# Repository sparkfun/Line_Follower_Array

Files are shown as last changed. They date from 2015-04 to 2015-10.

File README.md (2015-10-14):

SparkFun Line Follower Array
========================================

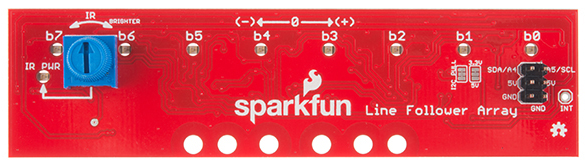
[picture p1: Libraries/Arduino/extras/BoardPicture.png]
SparkFun Line Follower Array


[*SparkFun Line Follower Array (SEN-13582)*](https://www.sparkfun.com/products/13582)

The Sensor Bar takes an 8 bit reading of reflectance for use with following lines or reading dark/light patterns.  The bar can see from about 1/4 to 3/4 inches away.  IR illumination power can be adjusted with the on-board potentiometer.  Illumination can be turned on and off with software to conserve power, or left on all the time for faster readings.

Repository Contents
-------------------

* **/Documentation** - Data sheets, additional product information
* **/Hardware** - Eagle design files (.brd, .sch)
* **/Libraries** - Libraries for use with the RedBot Line Follower Sensor Bar
* **/Production** - Production panel files (.brd)

Documentation
--------------
* **[Library](https://github.com/sparkfun/SparkFun_Line_Follower_Array_Arduino_Library)** - Arduino library for the array.
* **[Hookup Guide](https://learn.sparkfun.com/tutorials/sparkfun-line-follower-array-hookup-guide)** - Basic hookup guide for the array.

Product Versions
----------------
* [*SparkFun Line Follower Array (SEN-13582)*](https://www.sparkfun.com/products/13582)

Version History
---------------
* [V_0.4.0](https://github.com/sparkfun/Line_Follower_Array/tree/V_0.4.0) - Last proto version 
* [V_1.0.0](https://github.com/sparkfun/Line_Follower_Array/tree/V_1.0.0) - Release version

License Information
-------------------

This product is _**open source**_! 

Please review the LICENSE.md file for license information. 

If you have any questions or concerns on licensing, please contact techsupport@sparkfun.com.

Distributed as-is; no warranty is given.

- Your friends at SparkFun.

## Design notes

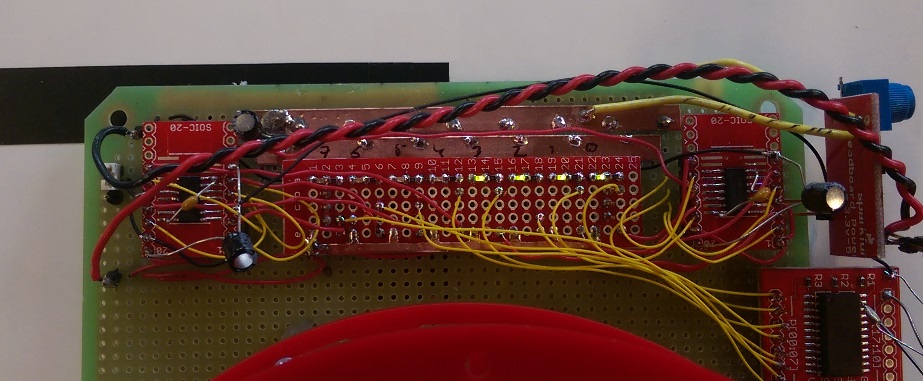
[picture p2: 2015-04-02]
Pictures/left4.jpg

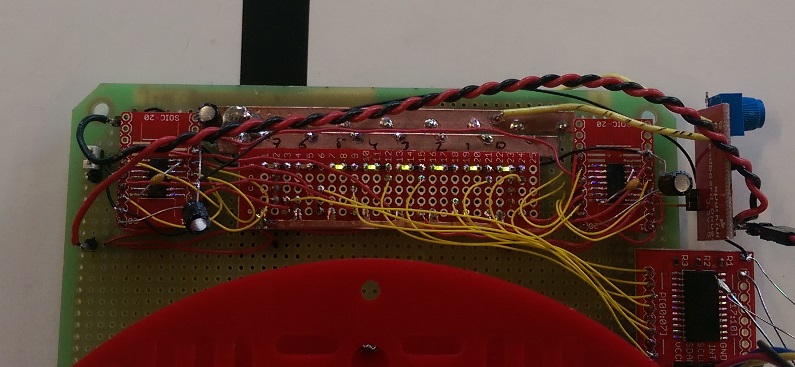
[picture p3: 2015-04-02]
Pictures/left2.jpg

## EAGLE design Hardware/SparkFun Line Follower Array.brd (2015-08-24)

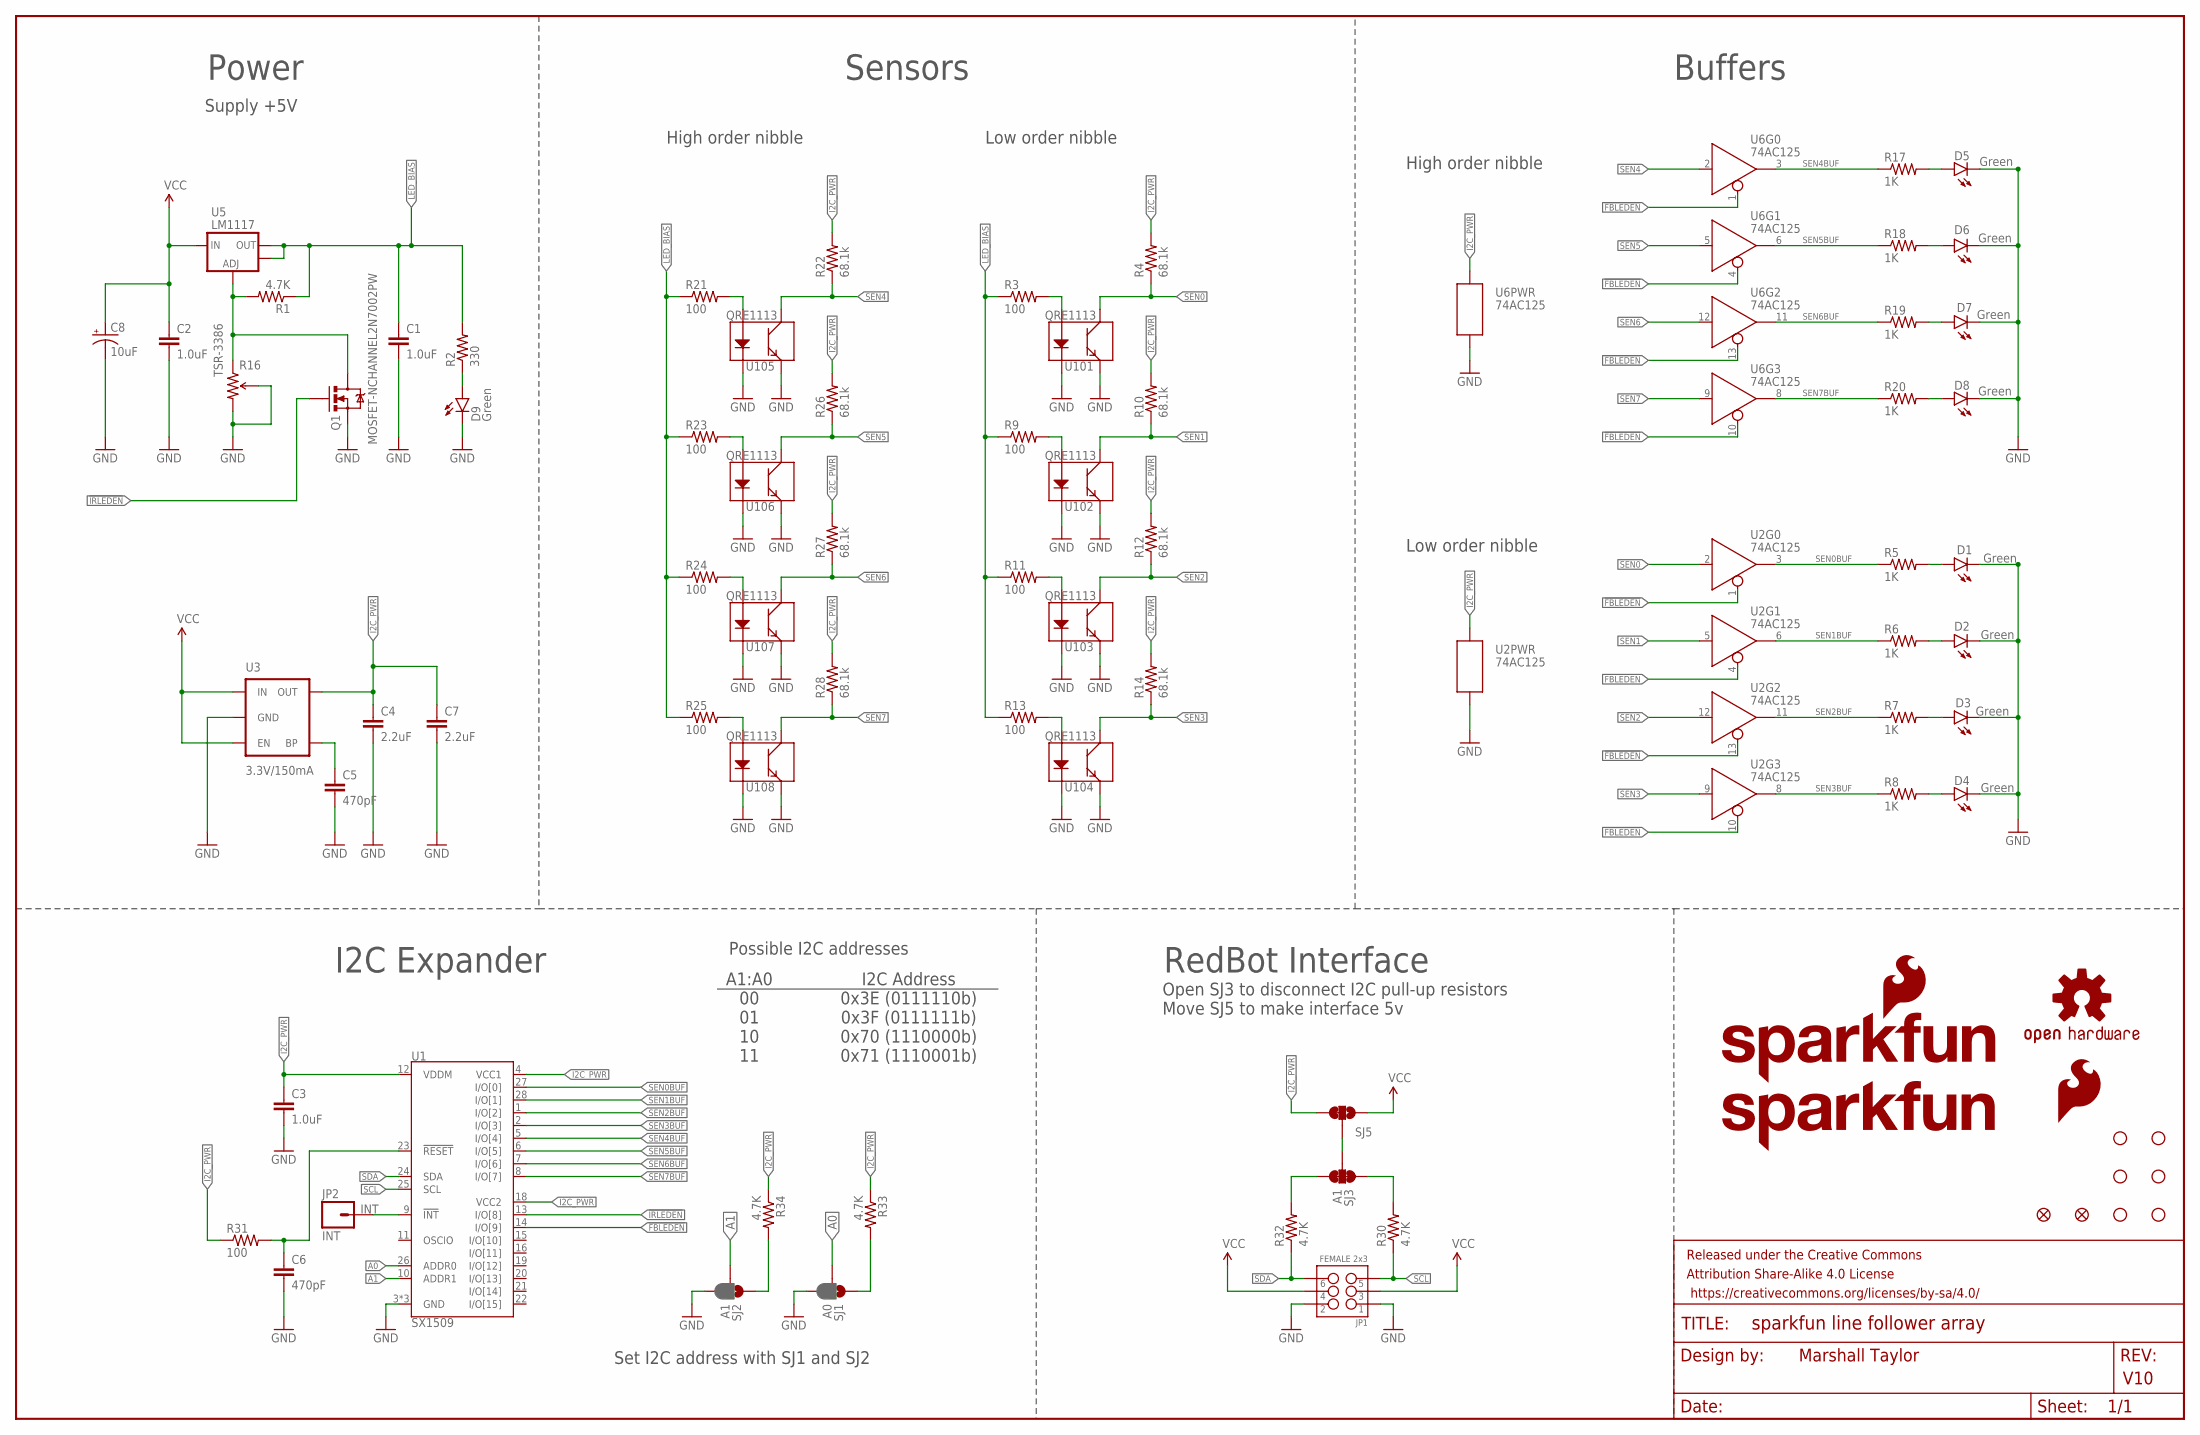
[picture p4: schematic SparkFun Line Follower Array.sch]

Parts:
C1, C2, C3: 1.0uF; 0603-CAP
C4, C7: 2.2uF; 0603-CAP
C5, C6: 470pF; 0603-CAP
C8: 10uF; EIA3216
D1, D2, D3, D4, D5, D6, D7, D8, D9: Green; LED-1206-BOTTOM
FID1, FID2: FIDUCIALUFIDUCIAL; MICRO-FIDUCIAL
FRAME2: FRAME-LEDGER; CREATIVE_COMMONS
JP1: FEMALE 2x3; 2X3
JP2: INT; 1X01
LOGO1: SFE_LOGO_NAME_FLAME.2_INCH; SFE_LOGO_NAME_FLAME_.2
LOGO2: SFE_LOGO_NAME.2_INCH; SFE_LOGO_NAME_.2
LOGO5: SFE_LOGO_FLAME.3_INCH; SFE_LOGO_FLAME_.3
LOGO6: OSHW-LOGOS; OSHW-LOGO-S
Q1: MOSFET-NCHANNEL2N7002PW; SOT323
R1, R30, R32, R33, R34: 4.7K; 0603-RES
R2: 330; 0603-RES
R3, R9, R11, R13, R21, R23, R24, R25, R31: 100; 0603-RES
R4, R10, R12, R14, R22, R26, R27, R28: 68.1k; 0603-RES
R5, R6, R7, R8, R17, R18, R19, R20: 1K; 0603-RES
R16: TSR-3386; 3386U
SJ1: A0; PAD-JUMPER-3-2OF3_NC_BY_PASTE_YES_SILK_FULL_BOX
SJ2: A1; PAD-JUMPER-3-2OF3_NC_BY_PASTE_YES_SILK_FULL_BOX
SJ3: A1; PAD-JUMPER-3-3OF3_NC_BY_TRACE_YES_SILK_FULL_BOX
SJ5: JUMPER-PAD-3-2OF3_NC_BY_TRACE_SMALL; PAD-JUMPER-3-2OF3_NC_BY_TRACE_YES_SILK_FULL_BOX
STANDOFF1, STANDOFF2, STANDOFF3, STANDOFF4, STANDOFF5, STANDOFF6: STAND-OFF
U1: SX1509; QFN-28
U2, U6: 74AC125; SO14
U3: 3.3V/150mA; SOT23-5
U5: LM1117; SOT223
U101, U102, U103, U104, U105, U106, U107, U108: QRE1113

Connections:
!FBLEDEN: U1.14 (I/O[9]), U2.1 (!EN), U2.4 (!EN), U2.10 (!EN), U2.13 (!EN), U6.1 (!EN), U6.4 (!EN), U6.10 (!EN), U6.13 (!EN)
!IRLEDEN: Q1.1 (G), U1.13 (I/O[8])
A0: SJ1.2, U1.26 (ADDR0)
A1: SJ2.2, U1.10 (ADDR1)
GND: C1.2, C2.2, C3.2, C4.2, C5.2, C6.2, C7.2, C8.C (-), D1.C, D2.C, D3.C, D4.C, D5.C, D6.C, D7.C, D8.C, D9.C, JP1.1, JP1.2, Q1.2 (S), R16.2 (WIPER), R16.3 (CW), SJ1.3, SJ2.3, U1.3 (GND), U1.17 (GND), U1.29 (GND), U2.7 (P$V-), U3.2 (GND), U6.7 (P$V-), U101.2 (K), U101.4 (E), U102.2 (K), U102.4 (E), U103.2 (K), U103.4 (E), U104.2 (K), U104.4 (E), U105.2 (K), U105.4 (E), U106.2 (K), U106.4 (E), U107.2 (K), U107.4 (E), U108.2 (K), U108.4 (E)
I2C_PWR: C3.1, C4.1, C7.1, R4.2, R10.2, R12.2, R14.2, R22.2, R26.2, R27.2, R28.2, R31.1, R33.1, R34.1, SJ5.3, U1.4 (VCC1), U1.12 (VDDM), U1.18 (VCC2), U2.14 (P$V+), U3.5 (OUT), U6.14 (P$V+)
INT: JP2.1, U1.9 (!INT)
LED_BIAS: C1.1, R1.1, R2.2, R3.1, R9.1, R11.1, R13.1, R21.1, R23.1, R24.1, R25.1, U5.2 (OUT), U5.4 (OUT)
unnamed: Q1.3 (D), R1.2, R16.1 (CCW), U5.1 (ADJ)
unnamed: R3.2, U101.1 (A)
unnamed: R21.2, U105.1 (A)
unnamed: R30.2, SJ3.1
unnamed: D1.A, R5.2
unnamed: C5.1, U3.4 (BP)
unnamed: D2.A, R6.2
unnamed: R32.2, SJ3.3
unnamed: D3.A, R7.2
unnamed: R34.2, SJ2.1
unnamed: D4.A, R8.2
unnamed: R9.2, U102.1 (A)
unnamed: R23.2, U106.1 (A)
unnamed: R11.2, U103.1 (A)
unnamed: R24.2, U107.1 (A)
unnamed: R13.2, U104.1 (A)
unnamed: R25.2, U108.1 (A)
unnamed: D9.A, R2.1
unnamed: SJ3.2, SJ5.2
unnamed: D5.A, R17.2
unnamed: R33.2, SJ1.1
unnamed: D6.A, R18.2
unnamed: D7.A, R19.2
unnamed: D8.A, R20.2
SCL: JP1.5, R30.1, U1.25 (SCL)
SDA: JP1.6, R32.1, U1.24 (SDA)
SEN0: R4.1, U2.2 (D), U101.3 (C)
SEN0BUF: R5.1, U1.27 (I/O[0]), U2.3 (Q)
SEN1: R10.1, U2.5 (D), U102.3 (C)
SEN1BUF: R6.1, U1.28 (I/O[1]), U2.6 (Q)
SEN2: R12.1, U2.12 (D), U103.3 (C)
SEN2BUF: R7.1, U1.1 (I/O[2]), U2.11 (Q)
SEN3: R14.1, U2.9 (D), U104.3 (C)
SEN3BUF: R8.1, U1.2 (I/O[3]), U2.8 (Q)
SEN4: R22.1, U6.2 (D), U105.3 (C)
SEN4BUF: R17.1, U1.5 (I/O[4]), U6.3 (Q)
SEN5: R26.1, U6.5 (D), U106.3 (C)
SEN5BUF: R18.1, U1.6 (I/O[5]), U6.6 (Q)
SEN6: R27.1, U6.12 (D), U107.3 (C)
SEN6BUF: R19.1, U1.7 (I/O[6]), U6.11 (Q)
SEN7: R28.1, U6.9 (D), U108.3 (C)
SEN7BUF: R20.1, U1.8 (I/O[7]), U6.8 (Q)
VCC: C2.1, C8.A (+), JP1.3, JP1.4, SJ5.1, U3.1 (IN), U3.3 (EN), U5.3 (IN)
~RESET: C6.1, R31.2, U1.23 (!RESET)

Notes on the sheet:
Marshall Taylor
V10
Low order nibble
Supply +5V
Sensors
High order nibble
Buffers
Power
RedBot Interface
I2C Expander
Set I2C address with SJ1 and SJ2
Open SJ3 to disconnect I2C pull-up resistors Move SJ5 to make interface 5v
Possible I2C addresses
A1:A0 00 01 10 11
I2C Address 0x3E (0111110b) 0x3F (0111111b) 0x70 (1110000b) 0x71 (1110001b)

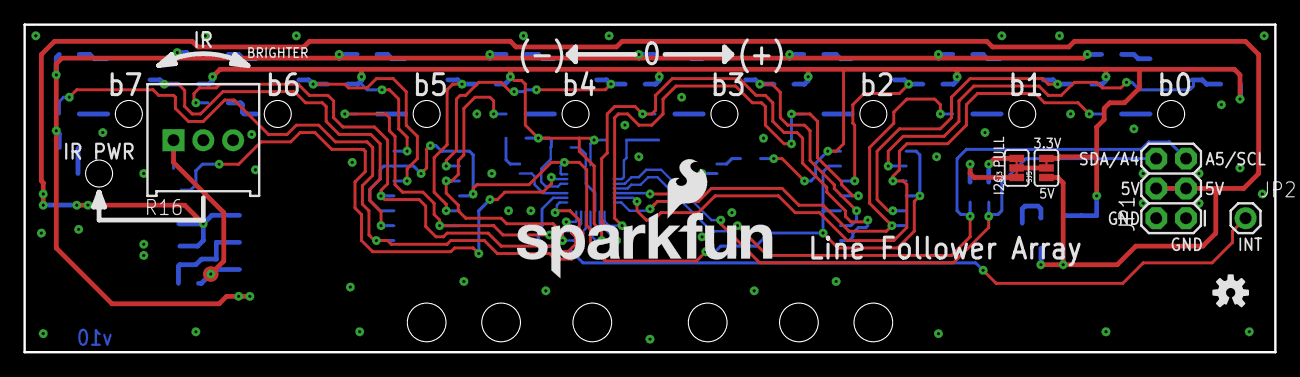
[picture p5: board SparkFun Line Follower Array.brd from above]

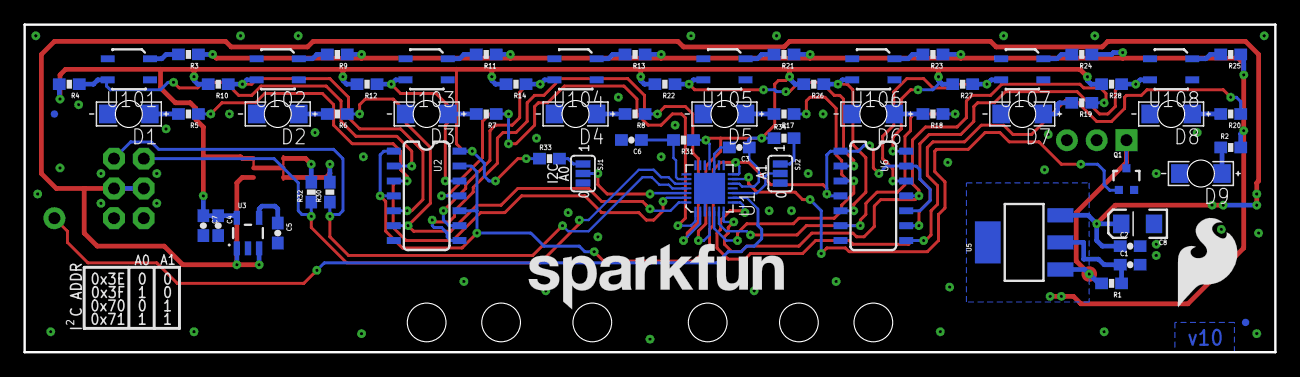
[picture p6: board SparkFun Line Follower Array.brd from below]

Board: 2 copper layers, 106.7 x 27.9 mm, 82 parts (68 on the bottom side), 52 nets.

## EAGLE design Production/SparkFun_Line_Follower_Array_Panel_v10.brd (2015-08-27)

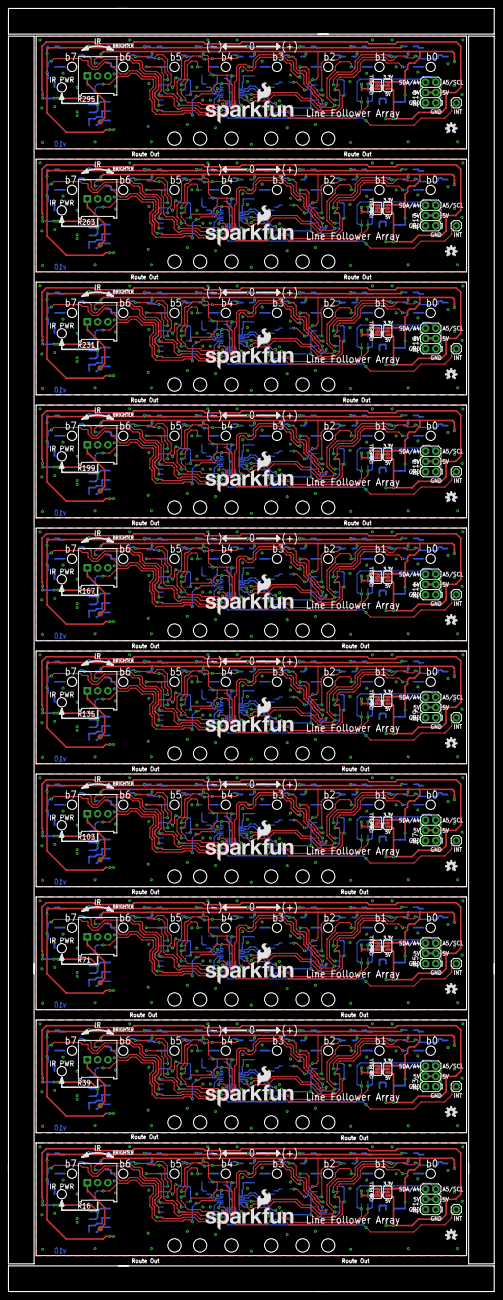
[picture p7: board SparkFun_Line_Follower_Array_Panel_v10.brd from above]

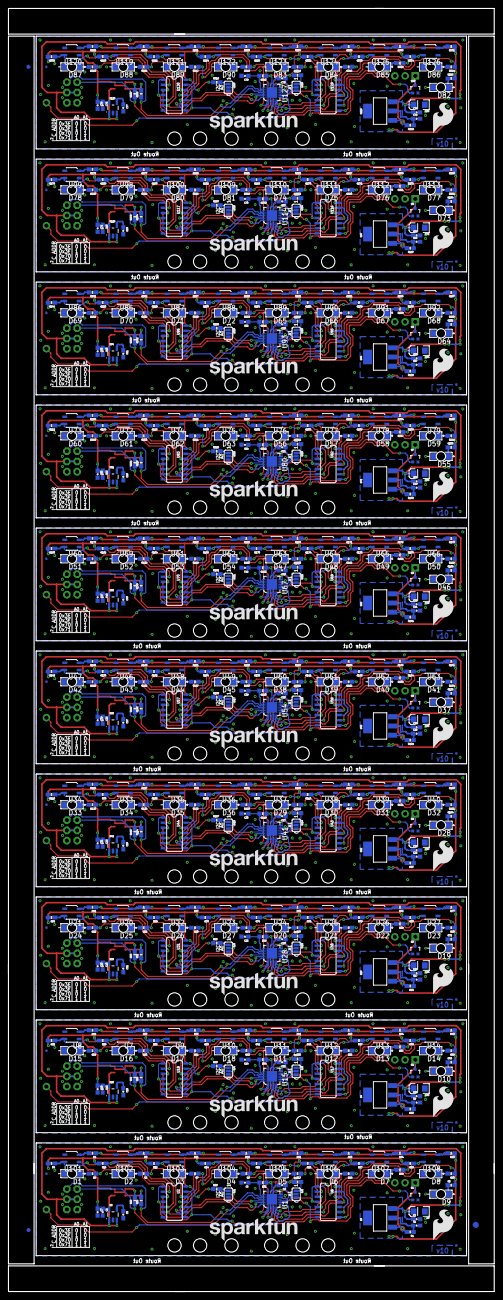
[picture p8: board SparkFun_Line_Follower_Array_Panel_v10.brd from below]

Board: 2 copper layers, 120.4 x 318.0 mm, 813 parts (683 on the bottom side), 520 nets.

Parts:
C1, C2, C3, C9, C10, C11, C17, C18, C19, C25, C26, C27, C33, C34, C35, C41, C42, C43, C49, C50, C51, C57, C58, C59, C65, C66, C67, C73, C74, C75: 1.0uF; 0603-CAP
C4, C7, C12, C15, C20, C23, C28, C31, C36, C39, C44, C47, C52, C55, C60, C63, C68, C71, C76, C79: 2.2uF; 0603-CAP
C5, C6, C13, C14, C21, C22, C29, C30, C37, C38, C45, C46, C53, C54, C61, C62, C69, C70, C77, C78: 470pF; 0603-CAP
C8, C16, C24, C32, C40, C48, C56, C64, C72, C80: 10uF; EIA3216
D1, D2, D3, D4, D5, D6, D7, D8, D9, D10, D11, D12, D13, D14, D15, D16, D17, D18, D19, D20, D21, D22, D23, D24, D25, D26, D27, D28, D29, D30, D31, D32, D33, D34, D35, D36, D37, D38, D39, D40, D41, D42, D43, D44, D45, D46, D47, D48, D49, D50, D51, D52, D53, D54, D55, D56, D57, D58, D59, D60, D61, D62, D63, D64, D65, D66, D67, D68, D69, D70, D71, D72, D73, D74, D75, D76, D77, D78, D79, D80, D81, D82, D83, D84, D85, D86, D87, D88, D89, D90: Green; LED-1206-BOTTOM
E$1: FIDUCIAL-1.5X3
E$5, E$6: FIDUCIAL-1X2
FID1, FID2, FID3, FID4, FID5, FID6, FID7, FID8, FID9, FID10, FID11, FID12, FID13, FID14, FID15, FID16, FID17, FID18, FID19, FID20: FIDUCIALUFIDUCIAL; MICRO-FIDUCIAL
JP1, JP3, JP5, JP7, JP9, JP11, JP13, JP15, JP17, JP19: FEMALE 2x3; 2X3
JP2, JP4, JP6, JP8, JP10, JP12, JP14, JP16, JP18, JP20: INT; 1X01
LOGO1, LOGO8, LOGO12, LOGO16, LOGO20, LOGO24, LOGO28, LOGO32, LOGO36, LOGO40: SFE_LOGO_NAME_FLAME.2_INCH; SFE_LOGO_NAME_FLAME_.2
LOGO2, LOGO3, LOGO9, LOGO13, LOGO17, LOGO21, LOGO25, LOGO29, LOGO33, LOGO37: SFE_LOGO_NAME.2_INCH; SFE_LOGO_NAME_.2
LOGO4, LOGO5, LOGO10, LOGO14, LOGO18, LOGO22, LOGO26, LOGO30, LOGO34, LOGO38: SFE_LOGO_FLAME.3_INCH; SFE_LOGO_FLAME_.3
LOGO6, LOGO7, LOGO11, LOGO15, LOGO19, LOGO23, LOGO27, LOGO31, LOGO35, LOGO39: OSHW-LOGOS; OSHW-LOGO-S
Q1, Q2, Q3, Q4, Q5, Q6, Q7, Q8, Q9, Q10: MOSFET-NCHANNEL2N7002PW; SOT323
R1, R15, R30, R32, R33, R34, R50, R51, R63, R64, R65, R82, R83, R95, R96, R97, R114, R115, R127, R128, R129, R146, R147, R159, R160, R161, R178, R179, R191, R192, R193, R210, R211, R223, R224, R225, R242, R243, R255, R256, R257, R274, R275, R287, R288, R289, R306, R307, R319, R320: 4.7K; 0603-RES
R2, R40, R72, R104, R136, R168, R200, R232, R264, R296: 330; 0603-RES
R3, R9, R11, R13, R21, R23, R24, R25, R31, R35, R37, R41, R43, R44, R45, R49, R53, R54, R67, R69, R73, R75, R76, R77, R81, R85, R86, R99, R101, R105, R107, R108, R109, R113, R117, R118, R131, R133, R137, R139, R140, R141, R145, R149, R150, R163, R165, R169, R171, R172, R173, R177, R181, R182, R195, R197, R201, R203, R204, R205, R209, R213, R214, R227, R229, R233, R235, R236, R237, R241, R245, R246, R259, R261, R265, R267, R268, R269, R273, R277, R278, R291, R293, R297, R299, R300, R301, R305, R309, R310: 100; 0603-RES
R4, R10, R12, R14, R22, R26, R27, R28, R29, R36, R38, R42, R46, R47, R48, R52, R66, R68, R70, R74, R78, R79, R80, R84, R98, R100, R102, R106, R110, R111, R112, R116, R130, R132, R134, R138, R142, R143, R144, R148, R162, R164, R166, R170, R174, R175, R176, R180, R194, R196, R198, R202, R206, R207, R208, R212, R226, R228, R230, R234, R238, R239, R240, R244, R258, R260, R262, R266, R270, R271, R272, R276, R290, R292, R294, R298, R302, R303, R304, R308: 68.1k; 0603-RES
R5, R6, R7, R8, R17, R18, R19, R20, R55, R56, R57, R58, R59, R60, R61, R62, R87, R88, R89, R90, R91, R92, R93, R94, R119, R120, R121, R122, R123, R124, R125, R126, R151, R152, R153, R154, R155, R156, R157, R158, R183, R184, R185, R186, R187, R188, R189, R190, R215, R216, R217, R218, R219, R220, R221, R222, R247, R248, R249, R250, R251, R252, R253, R254, R279, R280, R281, R282, R283, R284, R285, R286, R311, R312, R313, R314, R315, R316, R317, R318: 1K; 0603-RES
R16, R39, R71, R103, R135, R167, R199, R231, R263, R295: TSR-3386; 3386U
SJ1, SJ4, SJ9, SJ13, SJ17, SJ21, SJ25, SJ29, SJ33, SJ37: A0; PAD-JUMPER-3-2OF3_NC_BY_PASTE_YES_SILK_FULL_BOX
SJ2, SJ6, SJ10, SJ14, SJ18, SJ22, SJ26, SJ30, SJ34, SJ38: A1; PAD-JUMPER-3-2OF3_NC_BY_PASTE_YES_SILK_FULL_BOX
SJ3, SJ7, SJ11, SJ15, SJ19, SJ23, SJ27, SJ31, SJ35, SJ39: A1; PAD-JUMPER-3-3OF3_NC_BY_TRACE_YES_SILK_FULL_BOX
SJ5, SJ8, SJ12, SJ16, SJ20, SJ24, SJ28, SJ32, SJ36, SJ40: JUMPER-PAD-3-2OF3_NC_BY_TRACE_SMALL; PAD-JUMPER-3-2OF3_NC_BY_TRACE_YES_SILK_FULL_BOX
STANDOFF1, STANDOFF2, STANDOFF3, STANDOFF4, STANDOFF5, STANDOFF6, STANDOFF7, STANDOFF8, STANDOFF9, STANDOFF10, STANDOFF11, STANDOFF12, STANDOFF13, STANDOFF14, STANDOFF15, STANDOFF16, STANDOFF17, STANDOFF18, STANDOFF19, STANDOFF20, STANDOFF21, STANDOFF22, STANDOFF23, STANDOFF24, STANDOFF25, STANDOFF26, STANDOFF27, STANDOFF28, STANDOFF29, STANDOFF30, STANDOFF31, STANDOFF32, STANDOFF33, STANDOFF34, STANDOFF35, STANDOFF36, STANDOFF37, STANDOFF38, STANDOFF39, STANDOFF40, STANDOFF41, STANDOFF42, STANDOFF43, STANDOFF44, STANDOFF45, STANDOFF46, STANDOFF47, STANDOFF48, STANDOFF49, STANDOFF50, STANDOFF51, STANDOFF52, STANDOFF53, STANDOFF54, STANDOFF55, STANDOFF56, STANDOFF57, STANDOFF58, STANDOFF59, STANDOFF60: STAND-OFF
U1, U15, U28, U41, U54, U67, U80, U93, U114, U127: SX1509; QFN-28
U2, U6, U17, U18, U30, U31, U43, U44, U56, U57, U69, U70, U82, U83, U95, U96, U116, U117, U129, U130: 74AC125; SO14
U3, U16, U29, U42, U55, U68, U81, U94, U115, U128: 3.3V/150mA; SOT23-5
U4, U5, U19, U32, U45, U58, U71, U84, U97, U118: LM1117; SOT223
U7, U8, U9, U10, U11, U12, U13, U14, U20, U21, U22, U23, U24, U25, U26, U27, U33, U34, U35, U36, U37, U38, U39, U40, U46, U47, U48, U49, U50, U51, U52, U53, U59, U60, U61, U62, U63, U64, U65, U66, U72, U73, U74, U75, U76, U77, U78, U79, U85, U86, U87, U88, U89, U90, U91, U92, U98, U99, U100, U101, U102, U103, U104, U105, U106, U107, U108, U109, U110, U111, U112, U113, U119, U120, U121, U122, U123, U124, U125, U126: QRE1113

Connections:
!FBLEDEN: U1.14, U2.1, U2.4, U2.10, U2.13, U6.1, U6.4, U6.10, U6.13
!FBLEDEN1: U15.14, U17.1, U17.4, U17.10, U17.13, U18.1, U18.4, U18.10, U18.13
!FBLEDEN2: U28.14, U30.1, U30.4, U30.10, U30.13, U31.1, U31.4, U31.10, U31.13
!FBLEDEN3: U41.14, U43.1, U43.4, U43.10, U43.13, U44.1, U44.4, U44.10, U44.13
!FBLEDEN4: U54.14, U56.1, U56.4, U56.10, U56.13, U57.1, U57.4, U57.10, U57.13
!FBLEDEN5: U67.14, U69.1, U69.4, U69.10, U69.13, U70.1, U70.4, U70.10, U70.13
!FBLEDEN6: U80.14, U82.1, U82.4, U82.10, U82.13, U83.1, U83.4, U83.10, U83.13
!FBLEDEN7: U93.14, U95.1, U95.4, U95.10, U95.13, U96.1, U96.4, U96.10, U96.13
!FBLEDEN8: U114.14, U116.1, U116.4, U116.10, U116.13, U117.1, U117.4, U117.10, U117.13
!FBLEDEN9: U127.14, U129.1, U129.4, U129.10, U129.13, U130.1, U130.4, U130.10, U130.13
!IRLEDEN: Q1.1, U1.13
!IRLEDEN1: Q2.1, U15.13
!IRLEDEN2: Q3.1, U28.13
!IRLEDEN3: Q4.1, U41.13
!IRLEDEN4: Q5.1, U54.13
!IRLEDEN5: Q6.1, U67.13
!IRLEDEN6: Q7.1, U80.13
!IRLEDEN7: Q8.1, U93.13
!IRLEDEN8: Q9.1, U114.13
!IRLEDEN9: Q10.1, U127.13
A0: SJ1.2, U1.26
A1: SJ2.2, U1.10
A2: SJ4.2, U15.26
A3: SJ6.2, U15.10
A4: SJ9.2, U28.26
A5: SJ10.2, U28.10
A6: SJ13.2, U41.26
A7: SJ14.2, U41.10
A8: SJ17.2, U54.26
A9: SJ18.2, U54.10
A10: SJ21.2, U67.26
A11: SJ22.2, U67.10
A12: SJ25.2, U80.26
A13: SJ26.2, U80.10
A14: SJ29.2, U93.26
A15: SJ30.2, U93.10
A16: SJ33.2, U114.26
A17: SJ34.2, U114.10
A18: SJ37.2, U127.26
A19: SJ38.2, U127.10
GND: C1.2, C2.2, C3.2, C4.2, C5.2, C6.2, C7.2, C8.C, D1.C, D2.C, D3.C, D4.C, D5.C, D6.C, D7.C, D8.C, D9.C, JP1.1, JP1.2, Q1.2, R16.2, R16.3, SJ1.3, SJ2.3, U1.3, U1.17, U1.29, U2.7, U3.2, U6.7, U101.2, U101.4, U102.2, U102.4, U103.2, U103.4, U104.2, U104.4, U105.2, U105.4, U106.2, U106.4, U107.2, U107.4, U108.2, U108.4
GND2: C9.2, C10.2, C11.2, C12.2, C13.2, C14.2, C15.2, C16.C, D10.C, D11.C, D12.C, D13.C, D14.C, D15.C, D16.C, D17.C, D18.C, JP3.1, JP3.2, Q2.2, R39.2, R39.3, SJ4.3, SJ6.3, U7.2, U7.4, U8.2, U8.4, U9.2, U9.4, U10.2, U10.4, U11.2, U11.4, U12.2, U12.4, U13.2, U13.4, U14.2, U14.4, U15.3, U15.17, U15.29, U16.2, U17.7, U18.7
GND3: C17.2, C18.2, C19.2, C20.2, C21.2, C22.2, C23.2, C24.C, D19.C, D20.C, D21.C, D22.C, D23.C, D24.C, D25.C, D26.C, D27.C, JP5.1, JP5.2, Q3.2, R71.2, R71.3, SJ9.3, SJ10.3, U20.2, U20.4, U21.2, U21.4, U22.2, U22.4, U23.2, U23.4, U24.2, U24.4, U25.2, U25.4, U26.2, U26.4, U27.2, U27.4, U28.3, U28.17, U28.29, U29.2, U30.7, U31.7
GND4: C25.2, C26.2, C27.2, C28.2, C29.2, C30.2, C31.2, C32.C, D28.C, D29.C, D30.C, D31.C, D32.C, D33.C, D34.C, D35.C, D36.C, JP7.1, JP7.2, Q4.2, R103.2, R103.3, SJ13.3, SJ14.3, U33.2, U33.4, U34.2, U34.4, U35.2, U35.4, U36.2, U36.4, U37.2, U37.4, U38.2, U38.4, U39.2, U39.4, U40.2, U40.4, U41.3, U41.17, U41.29, U42.2, U43.7, U44.7
GND5: C33.2, C34.2, C35.2, C36.2, C37.2, C38.2, C39.2, C40.C, D37.C, D38.C, D39.C, D40.C, D41.C, D42.C, D43.C, D44.C, D45.C, JP9.1, JP9.2, Q5.2, R135.2, R135.3, SJ17.3, SJ18.3, U46.2, U46.4, U47.2, U47.4, U48.2, U48.4, U49.2, U49.4, U50.2, U50.4, U51.2, U51.4, U52.2, U52.4, U53.2, U53.4, U54.3, U54.17, U54.29, U55.2, U56.7, U57.7
GND6: C41.2, C42.2, C43.2, C44.2, C45.2, C46.2, C47.2, C48.C, D46.C, D47.C, D48.C, D49.C, D50.C, D51.C, D52.C, D53.C, D54.C, JP11.1, JP11.2, Q6.2, R167.2, R167.3, SJ21.3, SJ22.3, U59.2, U59.4, U60.2, U60.4, U61.2, U61.4, U62.2, U62.4, U63.2, U63.4, U64.2, U64.4, U65.2, U65.4, U66.2, U66.4, U67.3, U67.17, U67.29, U68.2, U69.7, U70.7
GND7: C49.2, C50.2, C51.2, C52.2, C53.2, C54.2, C55.2, C56.C, D55.C, D56.C, D57.C, D58.C, D59.C, D60.C, D61.C, D62.C, D63.C, JP13.1, JP13.2, Q7.2, R199.2, R199.3, SJ25.3, SJ26.3, U72.2, U72.4, U73.2, U73.4, U74.2, U74.4, U75.2, U75.4, U76.2, U76.4, U77.2, U77.4, U78.2, U78.4, U79.2, U79.4, U80.3, U80.17, U80.29, U81.2, U82.7, U83.7
GND8: C57.2, C58.2, C59.2, C60.2, C61.2, C62.2, C63.2, C64.C, D64.C, D65.C, D66.C, D67.C, D68.C, D69.C, D70.C, D71.C, D72.C, JP15.1, JP15.2, Q8.2, R231.2, R231.3, SJ29.3, SJ30.3, U85.2, U85.4, U86.2, U86.4, U87.2, U87.4, U88.2, U88.4, U89.2, U89.4, U90.2, U90.4, U91.2, U91.4, U92.2, U92.4, U93.3, U93.17, U93.29, U94.2, U95.7, U96.7
GND9: C65.2, C66.2, C67.2, C68.2, C69.2, C70.2, C71.2, C72.C, D73.C, D74.C, D75.C, D76.C, D77.C, D78.C, D79.C, D80.C, D81.C, JP17.1, JP17.2, Q9.2, R263.2, R263.3, SJ33.3, SJ34.3, U98.2, U98.4, U99.2, U99.4, U100.2, U100.4, U109.2, U109.4, U110.2, U110.4, U111.2, U111.4, U112.2, U112.4, U113.2, U113.4, U114.3, U114.17, U114.29, U115.2, U116.7, U117.7
GND10: C73.2, C74.2, C75.2, C76.2, C77.2, C78.2, C79.2, C80.C, D82.C, D83.C, D84.C, D85.C, D86.C, D87.C, D88.C, D89.C, D90.C, JP19.1, JP19.2, Q10.2, R295.2, R295.3, SJ37.3, SJ38.3, U119.2, U119.4, U120.2, U120.4, U121.2, U121.4, U122.2, U122.4, U123.2, U123.4, U124.2, U124.4, U125.2, U125.4, U126.2, U126.4, U127.3, U127.17, U127.29, U128.2, U129.7, U130.7
I2C_PWR: C3.1, C4.1, C7.1, R4.2, R10.2, R12.2, R14.2, R22.2, R26.2, R27.2, R28.2, R31.1, R33.1, R34.1, SJ5.3, U1.4, U1.12, U1.18, U2.14, U3.5, U6.14
I2C_PWR1: C11.1, C12.1, C15.1, R29.2, R36.2, R38.2, R42.2, R46.2, R47.2, R48.2, R52.2, R54.1, R63.1, R64.1, SJ8.3, U15.4, U15.12, U15.18, U16.5, U17.14, U18.14
I2C_PWR2: C19.1, C20.1, C23.1, R66.2, R68.2, R70.2, R74.2, R78.2, R79.2, R80.2, R84.2, R86.1, R95.1, R96.1, SJ12.3, U28.4, U28.12, U28.18, U29.5, U30.14, U31.14
I2C_PWR3: C27.1, C28.1, C31.1, R98.2, R100.2, R102.2, R106.2, R110.2, R111.2, R112.2, R116.2, R118.1, R127.1, R128.1, SJ16.3, U41.4, U41.12, U41.18, U42.5, U43.14, U44.14
I2C_PWR4: C35.1, C36.1, C39.1, R130.2, R132.2, R134.2, R138.2, R142.2, R143.2, R144.2, R148.2, R150.1, R159.1, R160.1, SJ20.3, U54.4, U54.12, U54.18, U55.5, U56.14, U57.14
I2C_PWR5: C43.1, C44.1, C47.1, R162.2, R164.2, R166.2, R170.2, R174.2, R175.2, R176.2, R180.2, R182.1, R191.1, R192.1, SJ24.3, U67.4, U67.12, U67.18, U68.5, U69.14, U70.14
I2C_PWR6: C51.1, C52.1, C55.1, R194.2, R196.2, R198.2, R202.2, R206.2, R207.2, R208.2, R212.2, R214.1, R223.1, R224.1, SJ28.3, U80.4, U80.12, U80.18, U81.5, U82.14, U83.14
I2C_PWR7: C59.1, C60.1, C63.1, R226.2, R228.2, R230.2, R234.2, R238.2, R239.2, R240.2, R244.2, R246.1, R255.1, R256.1, SJ32.3, U93.4, U93.12, U93.18, U94.5, U95.14, U96.14
I2C_PWR8: C67.1, C68.1, C71.1, R258.2, R260.2, R262.2, R266.2, R270.2, R271.2, R272.2, R276.2, R278.1, R287.1, R288.1, SJ36.3, U114.4, U114.12, U114.18, U115.5, U116.14, U117.14
I2C_PWR9: C75.1, C76.1, C79.1, R290.2, R292.2, R294.2, R298.2, R302.2, R303.2, R304.2, R308.2, R310.1, R319.1, R320.1, SJ40.3, U127.4, U127.12, U127.18, U128.5, U129.14, U130.14
INT: JP2.1, U1.9
INT1: JP4.1, U15.9
INT2: JP6.1, U28.9
INT3: JP8.1, U41.9
INT4: JP10.1, U54.9
INT5: JP12.1, U67.9
INT6: JP14.1, U80.9
INT7: JP16.1, U93.9
INT8: JP18.1, U114.9
INT9: JP20.1, U127.9
LED_BIAS: C1.1, R1.1, R2.2, R3.1, R9.1, R11.1, R13.1, R21.1, R23.1, R24.1, R25.1, U5.2, U5.4
LED_BIAS1: C9.1, R15.1, R35.1, R37.1, R40.2, R41.1, R43.1, R44.1, R45.1, R49.1, R53.1, U4.2, U4.4
LED_BIAS2: C17.1, R65.1, R67.1, R69.1, R72.2, R73.1, R75.1, R76.1, R77.1, R81.1, R85.1, U19.2, U19.4
LED_BIAS3: C25.1, R97.1, R99.1, R101.1, R104.2, R105.1, R107.1, R108.1, R109.1, R113.1, R117.1, U32.2, U32.4
LED_BIAS4: C33.1, R129.1, R131.1, R133.1, R136.2, R137.1, R139.1, R140.1, R141.1, R145.1, R149.1, U45.2, U45.4
LED_BIAS5: C41.1, R161.1, R163.1, R165.1, R168.2, R169.1, R171.1, R172.1, R173.1, R177.1, R181.1, U58.2, U58.4
LED_BIAS6: C49.1, R193.1, R195.1, R197.1, R200.2, R201.1, R203.1, R204.1, R205.1, R209.1, R213.1, U71.2, U71.4
LED_BIAS7: C57.1, R225.1, R227.1, R229.1, R232.2, R233.1, R235.1, R236.1, R237.1, R241.1, R245.1, U84.2, U84.4
LED_BIAS8: C65.1, R257.1, R259.1, R261.1, R264.2, R265.1, R267.1, R268.1, R269.1, R273.1, R277.1, U97.2, U97.4
LED_BIAS9: C73.1, R289.1, R291.1, R293.1, R296.2, R297.1, R299.1, R300.1, R301.1, R305.1, R309.1, U118.2, U118.4
unnamed: Q1.3, R1.2, R16.1, U5.1
unnamed: R3.2, U101.1
unnamed: R21.2, U105.1
unnamed: R30.2, SJ3.1
unnamed: D1.A, R5.2
unnamed: C5.1, U3.4
unnamed: D2.A, R6.2
unnamed: R32.2, SJ3.3
unnamed: D3.A, R7.2
unnamed: R34.2, SJ2.1
unnamed: D4.A, R8.2
unnamed: R9.2, U102.1
unnamed: R23.2, U106.1
unnamed: R11.2, U103.1
unnamed: R24.2, U107.1
unnamed: R13.2, U104.1
unnamed: R25.2, U108.1
unnamed: D9.A, R2.1
unnamed: SJ3.2, SJ5.2
unnamed: D5.A, R17.2
unnamed: R33.2, SJ1.1
unnamed: D6.A, R18.2
unnamed: Q2.3, R15.2, R39.1, U4.1
unnamed: D7.A, R19.2
unnamed: R49.2, U8.1
unnamed: D8.A, R20.2
unnamed: D15.A, R59.2
unnamed: D16.A, R60.2
unnamed: D17.A, R61.2
unnamed: D18.A, R62.2
unnamed: R53.2, U7.1
unnamed: R35.2, U9.1
unnamed: R37.2, U10.1
unnamed: D10.A, R40.1
unnamed: D11.A, R55.2
unnamed: D12.A, R56.2
unnamed: D13.A, R57.2
unnamed: D14.A, R58.2
unnamed: R41.2, U11.1
unnamed: R43.2, U12.1
unnamed: R44.2, U13.1
unnamed: R45.2, U14.1
unnamed: C13.1, U16.4
unnamed: R50.2, SJ7.1
unnamed: R51.2, SJ7.3
unnamed: SJ7.2, SJ8.2
unnamed: R64.2, SJ6.1
unnamed: R63.2, SJ4.1
unnamed: Q3.3, R65.2, R71.1, U19.1
unnamed: R81.2, U21.1
unnamed: D24.A, R91.2
unnamed: D25.A, R92.2
unnamed: D26.A, R93.2
unnamed: D27.A, R94.2
unnamed: R85.2, U20.1
unnamed: R67.2, U22.1
unnamed: R69.2, U23.1
unnamed: D19.A, R72.1
unnamed: D20.A, R87.2
unnamed: D21.A, R88.2
unnamed: D22.A, R89.2
unnamed: D23.A, R90.2
unnamed: R73.2, U24.1
unnamed: R75.2, U25.1
unnamed: R76.2, U26.1
unnamed: R77.2, U27.1
unnamed: C21.1, U29.4
unnamed: R82.2, SJ11.1
unnamed: R83.2, SJ11.3
unnamed: SJ11.2, SJ12.2
unnamed: R96.2, SJ10.1
unnamed: R95.2, SJ9.1
unnamed: Q4.3, R97.2, R103.1, U32.1
unnamed: R113.2, U34.1
unnamed: D33.A, R123.2
unnamed: D34.A, R124.2
unnamed: D35.A, R125.2
unnamed: D36.A, R126.2
unnamed: R117.2, U33.1
unnamed: R99.2, U35.1
unnamed: R101.2, U36.1
unnamed: D28.A, R104.1
unnamed: D29.A, R119.2
unnamed: D30.A, R120.2
unnamed: D31.A, R121.2
unnamed: D32.A, R122.2
unnamed: R105.2, U37.1
unnamed: R107.2, U38.1
unnamed: R108.2, U39.1
unnamed: R109.2, U40.1
unnamed: C29.1, U42.4
unnamed: R114.2, SJ15.1
unnamed: R115.2, SJ15.3
unnamed: SJ15.2, SJ16.2
unnamed: R128.2, SJ14.1
unnamed: R127.2, SJ13.1
unnamed: Q5.3, R129.2, R135.1, U45.1
unnamed: R145.2, U47.1
unnamed: D42.A, R155.2
unnamed: D43.A, R156.2
unnamed: D44.A, R157.2
unnamed: D45.A, R158.2
unnamed: R149.2, U46.1
unnamed: R131.2, U48.1
unnamed: R133.2, U49.1
unnamed: D37.A, R136.1
unnamed: D38.A, R151.2
unnamed: D39.A, R152.2
unnamed: D40.A, R153.2
unnamed: D41.A, R154.2
unnamed: R137.2, U50.1
unnamed: R139.2, U51.1
unnamed: R140.2, U52.1
unnamed: R141.2, U53.1
unnamed: C37.1, U55.4
unnamed: R146.2, SJ19.1
unnamed: R147.2, SJ19.3
unnamed: SJ19.2, SJ20.2
unnamed: R160.2, SJ18.1
unnamed: R159.2, SJ17.1
unnamed: Q6.3, R161.2, R167.1, U58.1
unnamed: R177.2, U60.1
unnamed: D51.A, R187.2
unnamed: D52.A, R188.2
unnamed: D53.A, R189.2
unnamed: D54.A, R190.2
unnamed: R181.2, U59.1
unnamed: R163.2, U61.1
unnamed: R165.2, U62.1
unnamed: D46.A, R168.1
unnamed: D47.A, R183.2
unnamed: D48.A, R184.2
unnamed: D49.A, R185.2
unnamed: D50.A, R186.2
unnamed: R169.2, U63.1
unnamed: R171.2, U64.1
unnamed: R172.2, U65.1
unnamed: R173.2, U66.1
unnamed: C45.1, U68.4
unnamed: R178.2, SJ23.1
unnamed: R179.2, SJ23.3
unnamed: SJ23.2, SJ24.2
unnamed: R192.2, SJ22.1
unnamed: R191.2, SJ21.1
unnamed: Q7.3, R193.2, R199.1, U71.1
unnamed: R209.2, U73.1
unnamed: D60.A, R219.2
unnamed: D61.A, R220.2
unnamed: D62.A, R221.2
unnamed: D63.A, R222.2
unnamed: R213.2, U72.1
unnamed: R195.2, U74.1
unnamed: R197.2, U75.1
unnamed: D55.A, R200.1
unnamed: D56.A, R215.2
unnamed: D57.A, R216.2
unnamed: D58.A, R217.2
unnamed: D59.A, R218.2
unnamed: R201.2, U76.1
unnamed: R203.2, U77.1
unnamed: R204.2, U78.1
unnamed: R205.2, U79.1
unnamed: C53.1, U81.4
unnamed: R210.2, SJ27.1
unnamed: R211.2, SJ27.3
unnamed: SJ27.2, SJ28.2
unnamed: R224.2, SJ26.1
unnamed: R223.2, SJ25.1
unnamed: Q8.3, R225.2, R231.1, U84.1
unnamed: R241.2, U86.1
unnamed: D69.A, R251.2
unnamed: D70.A, R252.2
unnamed: D71.A, R253.2
unnamed: D72.A, R254.2
unnamed: R245.2, U85.1
unnamed: R227.2, U87.1
unnamed: R229.2, U88.1
unnamed: D64.A, R232.1
unnamed: D65.A, R247.2
unnamed: D66.A, R248.2
unnamed: D67.A, R249.2
unnamed: D68.A, R250.2
unnamed: R233.2, U89.1
unnamed: R235.2, U90.1
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

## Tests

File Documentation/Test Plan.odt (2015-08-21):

# Functional Testing Plan

## Code Things to Verify

- Detected patterns correctly become raw readings
- IR enb and Feedback indictors can be controlled
- I2C @ 100 KHz
- All address options function with driver

## HW Things to Verify

- Silkscreen axes for polarity
- Power consumption
  - With knob to min
  - With knob to max
  - Measure the current draw during a strobe with knob at max, Vbulk = 6v.
- I2C interface rise times are far below clk pulse high width
- MICxxxx regulators vend stable rails, does the cap need to be removed?

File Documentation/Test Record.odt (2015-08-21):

# Functional Test Record

Marshall Taylor

8/21/2015

## Readback Function

Procedure:

1. Use ReadBarOnly to sample the input once per second.
2. Set the knob to mid value

Criteria:

1. Do changes under each eye produce the correct change in the raw byte? YES
2. Do the vector readbacks match the silkscreen polarity/axis? YES

## Light Control Function

Procedure:

1. Attach a scope to LED_BIAS and FBLEDEN.
2. Run ReadBarOnly
3. Capture a read operation

Criteria:

1. Does the LED_BIAS pulse during read? YES
2. Does the FBLEDEN pulse 2ms after LED_BIAS? YES
3. Do they cutoff together? YES

## Addressing

Procedure:

1. Test the default configuration
2. Change the solder jumpers
3. Change the sketch to match the new configuration
4. Test the new configuration
5. Do for all 4 configurations

Criteria:

1. Did the code address values match the jumper silkscreen addresses? YES
2. Does the silkscreen box agree with the jumper silkscreen? NO

## Power Consumption

Procedure:

1. Connect an inline resistor of 0.1 to 0.5 ohm in the ground return path of the sensor bar
2. Record resistor value: 0.33 ohms
3. Power the redbot from 6.0 volts
4. Attach a scope across the resistor
5. Run ReadBarOnly
6. Set knob to max
7. Capture a read pulse
8. Record the quiescent voltage: 0.004 V
9. Record the peak voltagae: 0.072 V
10. Capture the scope view
11. Set knob to 1/2
12. Record the peak voltage: 0.042 V
13. Capture the scope view
14. Set knob to min
15. Record the peak voltagae: 0.004 V
16. Capture the scope view

Criteria:

1. Does the current jump up as a step function?: YES
2. Is the quiescent current 10mA +/- 20%? Calculate it: 12.1mA
3. Is max peak current 200mA +/- 20%? Calculate it: 218mA
4. Is mid peak current about 1/2 max? Calculate it: 127mA
5. Is the min peak current same as quiescent? YES

## I2C Signal Integrity

Procedure:

1. Attach scope probes to SDA and SCL with the shortest wire possible
2. Capture a full operation
3. Capture a zoom of 3 consecutively toggling SDA bits

Criteria:

1. Are I2C interface rise times are far below clk pulse high width?
2. Record the pullup resistor value as measured:
- 1: 4.565 kOhm
- 2: 4.587 kOhm

## MICxxxx rail stability

Procedure:

1. Look for ramp waveforms on the MICxxxx's output pin.

Criteria:

1. Is the bypass cap present? No
2. Does the MICxxxx benifit from removing the PB pin bypass cap? It did!

## Action Items

1. Change out pullups – 10k becomes 4.7k DONE
2. Add SDA and SCK silk to A4/A5 DONE
3. addr box confusing. Switch bit positions and lable individual columns DONE

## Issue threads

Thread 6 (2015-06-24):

No 2x3 header placement

marshalltaylorSFE, 2015-06-24:
Get a new part in the assembly.  Try the one from the FreeSoC

ToniCorinne, 2016-01-11:
Issue was fixed before release. Closing this out.

Closed 2016-01-11.

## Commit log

2015-03-18 added a couple more sketches. May remove in the future
2015-03-19 added first schematic part
    [8eye line sensor.sch]
2015-03-31 Layout commit
    [8eye line sensor.brd, 8eye line sensor.sch]
2015-04-07 Shrunk PCB
    [8eye line sensor.brd, 8eye line sensor.sch]
2015-04-08 logos and 47 measures and t_place added, Oh my!
    [8eye line sensor.brd, 8eye line sensor.sch]
2015-04-08 about ready for proto submit
    [8eye line sensor.brd, 8eye line sensor.sch]
2015-04-09 fixed for QC
    [8eye line sensor.brd, 8eye line sensor.sch]
2015-05-29 fixed half the issues
    [8eye line sensor.brd, 8eye line sensor.sch]
2015-05-29 Ran DRC, fixing aesthetic
    [8eye line sensor.brd]
2015-05-29 ready for review of prototype 2 (v03)
    [8eye line sensor.brd, 8eye line sensor.sch]
2015-06-01 Ready for proto
    [8eye line sensor.brd, 8eye line sensor.sch]
2015-06-04 Fixed github/qc finds
    [8eye line sensor.brd, 8eye line sensor.sch]
2015-07-09 v04: IR LED power ctrl, regulated receiver supply
    [8eye line sensor.brd, 8eye line sensor.sch]
2015-07-09 Fixed QC issues
    [8eye line sensor.brd, 8eye line sensor.sch]
2015-08-21 V_1.0 update
    [8eye line sensor.brd, 8eye line sensor.sch]
2015-08-21 Fixed rev number and readme
    [8eye line sensor.brd, 8eye line sensor.sch]
2015-08-24 Renamed project
    [SparkFun Line Follower Array.brd, SparkFun Line Follower Array.sch]
2015-08-27 created panel v10
    [SparkFun_Line_Follower_Array_Panel_v10.brd]
2015-10-14 Squashed 'Libraries/Arduino/' content from commit 02afd32
    git-subtree-dir: Libraries/Arduino
    git-subtree-split: 02afd32d755ee1969facbfc80f71514770557b3f
2016-01-11 Squashed 'Libraries/Arduino/' changes from 02afd32..2914662
    git-subtree-split: 29146627b9eda56a58f48e0abae9e124bb2415a8
    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

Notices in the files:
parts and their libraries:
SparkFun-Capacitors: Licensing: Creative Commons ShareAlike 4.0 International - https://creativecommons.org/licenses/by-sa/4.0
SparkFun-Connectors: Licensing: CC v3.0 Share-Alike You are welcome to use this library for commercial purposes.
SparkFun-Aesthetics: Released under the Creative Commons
